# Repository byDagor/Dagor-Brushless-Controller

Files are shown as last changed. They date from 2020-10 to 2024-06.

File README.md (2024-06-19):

# Dagor Brushless Controller

The Dagor Controller is a fully integrated tiny solution for brushless-based actuators with wireless capabilities and three operation modes: angular position, velocity and torque. It is an ESP32-based brushless controller that has an on-board magnetic encoder, a three-phase MOSFET driver, three MOSFET half-bridges, a temperature sensor and current sensing resistors.

> 📢 DOCUMENATION WEBSITE: https://docs.dagor.dev/

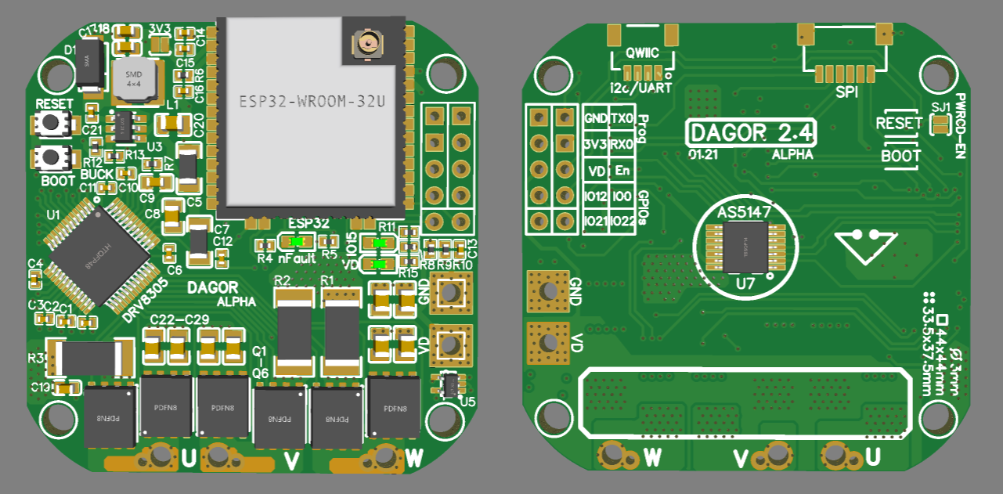
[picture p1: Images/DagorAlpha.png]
DagorBoard


## Key specs
| Specification | Rating |
| --- |:---:|
| Dimensions | 44 x 44mm |
| Mass | 12g |
| Power source voltage | 5-24V |
| Peak rms current | up to 40A |
| Magnetic sensor resolution | 14 bits |
| Temperature sensor range | -10 ~ 120°C |

> Note: The project is STILL currently on it’s Alpha stage and with the help of the Alpha testers the project will move forward faster.

## What makes this Controller different?
The *Dagor Brushless Controller* was designed as a simple platform for hobbyist and students to power brushless-based projects. This board offers wired and wireless connectivity modes to accommodate a variety of different kinds of projects. The firmware for this board was developed for the Arduino development environment and powered by the [SimpleFOC project](simplefoc.com). This code is merely a starting point as it’s encouraged to modify it to fit specific projects. The firmware being very easy to modify and understand gives some key advantages:

- great platform for single board projects
- custom communication schemes for multi-board projects
- implementation of unique control laws
- endless amount of compatible libraries

## HW Revisions
| Reivision | Changes |
| --- |:---:|
| 2.7 | Solid GND plane, input TVS diode. |
| 2.6 | Rearrenged the LEDs to avoid bleed, added extra bulk capacitance to the back. |

## Firmware Roadmap
- [x] Torque/ current control mode
- [ ] PWM input control
- [x] Full fault diagnostics report
- [ ] DRV8305 communication library
- [ ] Deep-sleep mode
- [ ] Save calibration parameters in ESP32's EEPROM
- [ ] Stall detection algorithm
- [ ] Finish RS-485-based protocol, directional comms working
- [ ] Virtual walls algorithm
- [ ] Detect DRV warnings vs. errors
- [ ] Make nicer out of bounds behavior
- [ ] Finish implementing state machine
- [ ] Change "H" homing command to accept home as arbitrary number or current position
- [ ] OTA Update
- [ ] Status LED blink patterns

## Contact
david@simplefoc.com 
[Linkedin](https://www.linkedin.com/in/david-g-reyes/)  
[YouTube](https://www.youtube.com/channel/UC4gsPZan2T4v5LpJ5J_t7sQ/featured)

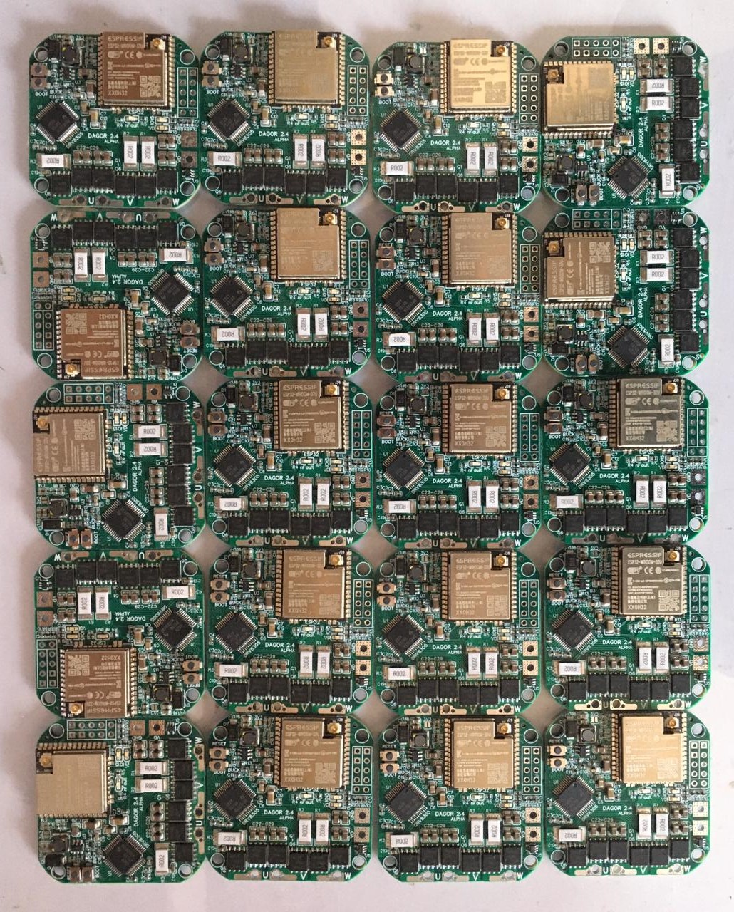
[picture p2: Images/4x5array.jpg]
array


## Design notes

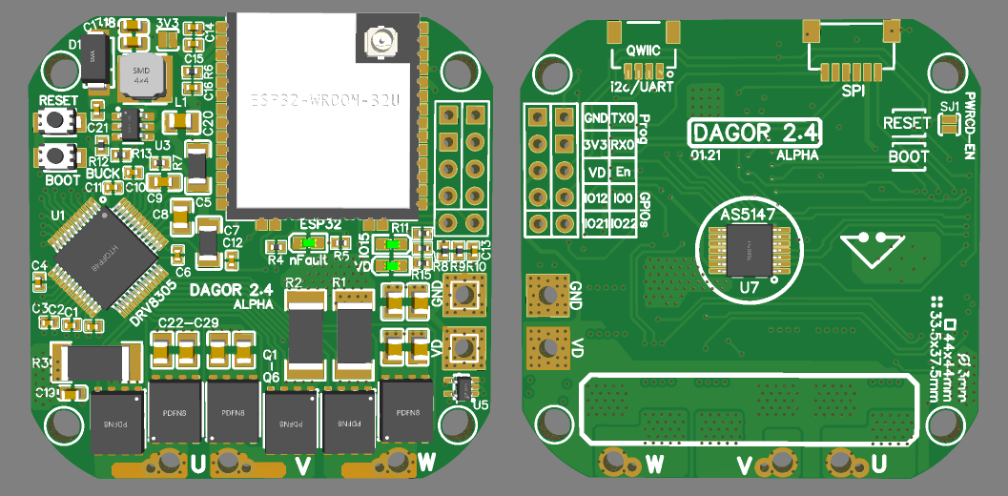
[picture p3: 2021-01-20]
Images/DagorAlpha2.4.png

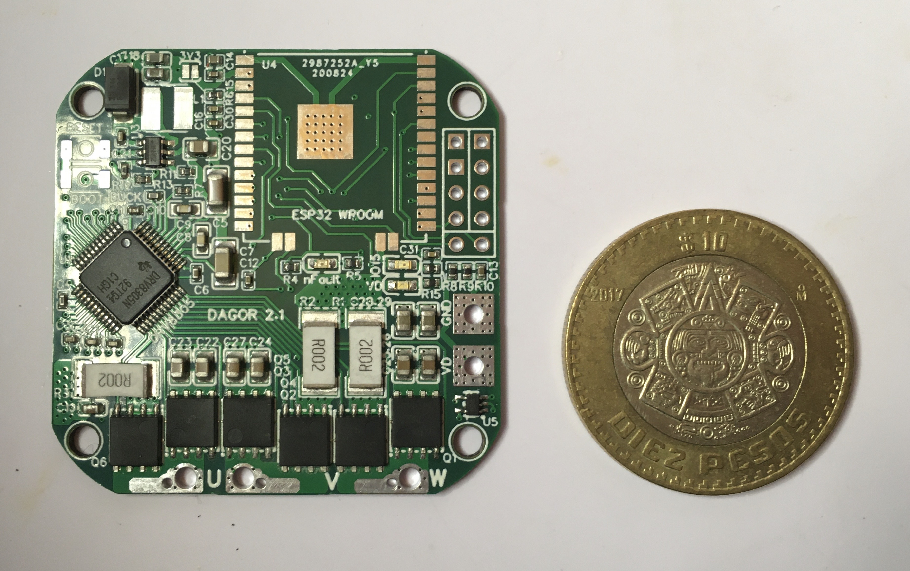
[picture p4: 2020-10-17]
Images/Size reference.JPG

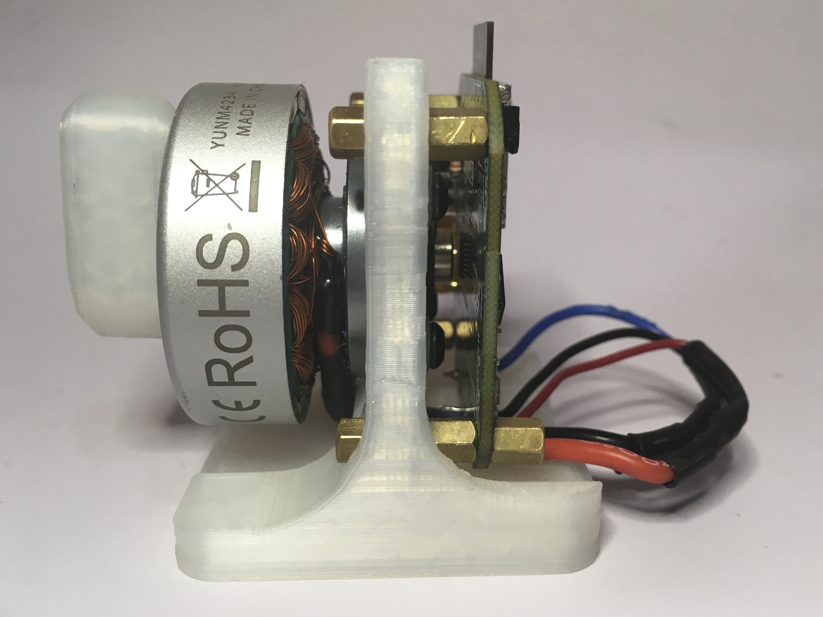
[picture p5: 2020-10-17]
Images/Side View.JPG

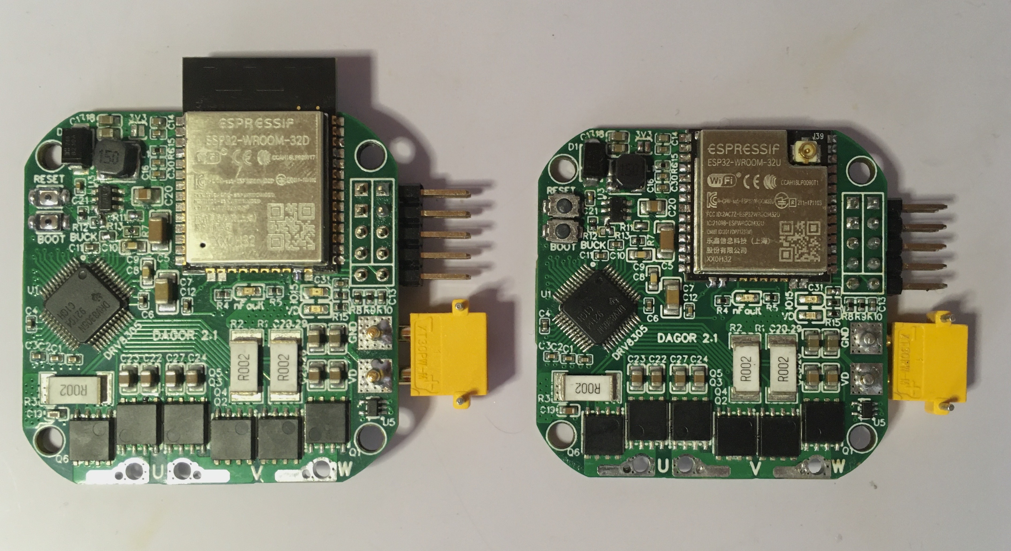
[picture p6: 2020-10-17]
Images/ESP32 Wroom U and D.JPG

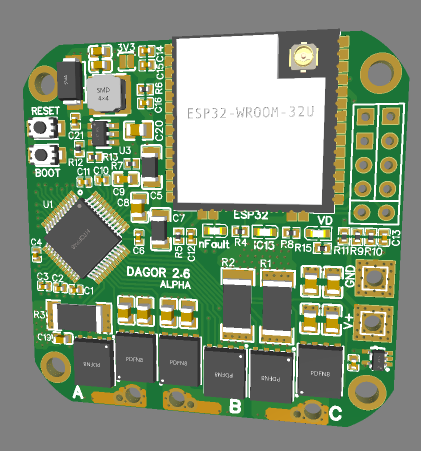
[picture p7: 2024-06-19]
Images/Dagor 2.6.PNG

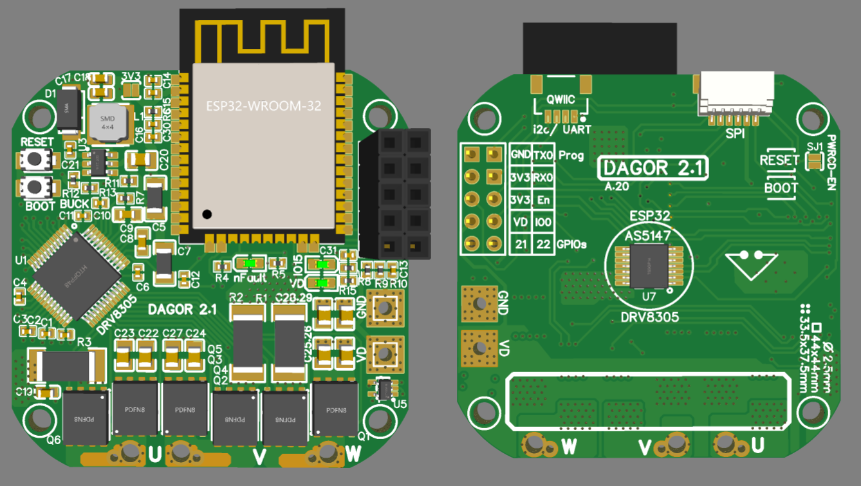
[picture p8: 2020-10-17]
Images/Dagor2.1.png

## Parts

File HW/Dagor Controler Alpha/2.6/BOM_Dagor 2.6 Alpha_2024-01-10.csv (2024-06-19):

ID | Name | Designator | Footprint | Quantity | Manufacturer Part | Manufacturer | Supplier | Supplier Part | Price
1 | 1nF | C1,C2,C3,C13 | C0402 | 4 | 0402B102K500NT | FH | LCSC | C1523 | 0.001
2 | 1uF | C4,C6,C10,C11 | C0402 | 4 | CL05A105KA5NQNC | SAMSUNG | LCSC | C52923 | 0.004
3 | 4.7uF | C5 | C1206 | 1 | 1206B475K500NT | FH | LCSC | C29823 | 0.031
4 | 2.2uF | C7 | C1206 | 1 | CL31B225KBHNNNE | SAMSUNG | LCSC | C50254 | 0.027
5 | 47nF | C8 | C0805 | 1 | CL21B473KCFNNNE | SAMSUNG | LCSC | C17074 | 0.02
6 | 47nF | C9 | C0603 | 1 | CL10B473KB8NNNC | SAMSUNG | LCSC | C1622 | 0.005
7 | 100nF | C12,C15,C16,C21,C30 | C0402 | 5 | CL05B104KO5NNNC | SAMSUNG | LCSC | C1525 | 0.001
8 | 10uF | C14 | C0402 | 1 | CL05A106MQ5NUNC | SAMSUNG | LCSC | C15525 | 0.005
9 | 22uF | C17 | C0603 | 1 | CL10A226MQ8NRNC | SAMSUNG | LCSC | C59461 | 0.008
10 | 10uF | C18 | C0603 | 1 | CL10A106MA8NRNC | SAMSUNG | LCSC | C96446 | 0.018
11 | 1uF | C19 | C0603 | 1 | CL10A105KB8NNNC | SAMSUNG | LCSC | C15849 | 0.005
12 | 10uF | C20,C22,C23,C24,C25,C26,C27,C28,C29,C31,C32,C33,C34,C35,C36,C39 | C0805 | 16 | GRM21BR61H106KE43L | Murata Electronics | LCSC | C440198 | 0.071
13 | 10uF | C37,C38 | C1206 | 2 | 1206X106M500NT | Guangdong Fenghua Advanced Tech | LCSC | C170075 | 0.045
14 | B230A-13-F | D1 | SMA_L4.4-W2.6-LS5.0-RD | 1 | B230A-13-F | DIODES | LCSC | C12889 | 0.072
15 | 15uH | L1 | IND-SMD_L4.0-W4.0 | 1 | PIS3D18P-150M-T | EMTEK | LCSC | C251755 | 0.228
16 | RED | LED1 | LED0603-R-RD | 1 | KT-0603R | KENTO | LCSC | C2286 | 0.006
17 | Blue | LED2 | LED0603-R-RD | 1 | 19-217/BHC-ZL1M2RY/3T | EVERLIGHT | LCSC | C72041 | 0.018
18 | Yellow | LED3 | LED0603-R-RD | 1 | 19-213/Y2C-CQ2R2L/3T(CY) | EVERLIGHT | LCSC | C72038 | 0.021
19 | TPH4R008 | Q1,Q2,Q3,Q4,Q5,Q6 | POWERVDFN-8_L6.2-W5.2-P1.27-LS6.0-BL | 6 | TPH4R008NH,L1Q(M | TOSHIBA | LCSC | C396039 | 1.22
20 | 0.002 | R1,R2,R3 | R2512 W/ KELVIN | 3 | MS122WF200NT4E | UniOhm | LCSC | C60923 | 0.095
21 | 330 | R4,R8 | R0402 | 2 | 0402WGF3300TCE | UniOhm | LCSC | C25104 | 0.001
22 | 10K | R5,R6,R11 | R0402 | 3 | 0402WGF1002TCE | UniOhm | LCSC | C25744 | 0.001
23 | 100 | R7 | R0402 | 1 | 0402WGF1000TCE | UniOhm | LCSC | C25076 | 0.001
24 | 33K | R9 | R0402 | 1 | 0402WGF2402TCE | UniOhm | LCSC | C25769 | 0.001
25 | 3.3K | R10 | R0402 | 1 | 0402WGF3301TCE | UniOhm | LCSC | C25890 | 0.001
26 | 110K | R12 | R0402 | 1 | NQ02WGF1103TCE | Uniroyal Elec | LCSC | C270379 | 0.002
27 | 33K | R13 | R0402 | 1 | 0402WGF3302TCE | UniOhm | LCSC | C25779 | 0.001
28 | 2.2K | R15 | R0402 | 1 | 0402WGF2201TCE | UniOhm | LCSC | C25879 | 0.001
29 | BOOT | SW1 | SW2-2.6-3.0X2.5X1.2+0.4MM | 1 | TS342A2P-WZ | SHOU HAN | LCSC | C557591 | 0.032
30 | RESET | SW2 | SW2-2.6-3.0X2.5X1.2+0.4MM | 1 | TS342A2P-WZ | SHOU HAN | LCSC | C557591 | 0.032
31 | DRV8305NPHPR | U1 | HTQFP-48_L7.0-W7.0-P0.50-LS9.0-BL-EP | 1 | DRV8305NPHPR | Texas Instruments | LCSC | C75602 | 254.25
32 | LMR14010ADDCR | U3 | SOT-23-6_L2.9-W1.6-P0.95-LS2.8-BR | 1 | LMR14010ADDCR | Texas Instruments | LCSC | C388174 | 0.934
33 | ESP-WROOM-32 | U4 | ESP-WROOM-32-NO-JTAG | 1 | ESP-WROOM-32 | ESPRESSIF | LCSC | C95209
34 | STLM20W87F | U5 | SOT-323-5_L2.1-W1.3-P0.65-LS2.1-BL | 1 | STLM20W87F | STMicroelectronics | LCSC | C129796 | 1.007
35 | AS5147P-HTSM | U7 | TSSOP-14_L5.0-W4.4-P0.65-LS6.5-BL | 1 | AS5147P-HTSM | Advanced Monolithic Systems | LCSC | C481876 | 21.449

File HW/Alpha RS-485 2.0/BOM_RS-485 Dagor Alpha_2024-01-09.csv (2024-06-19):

ID | Name | Designator | Footprint | Quantity | Manufacturer Part | Manufacturer | Supplier | Supplier Part | Price
1 | 100nF | C1 | C0402 | 1 | CL05B104KO5NNNC | SAMSUNG | LCSC | C1525 | 0.001
2 | 10uF | C2,C3,C4,C5 | C1206 | 4 | 1206X106M500NT | Guangdong Fenghua Advanced Tech | LCSC | C170075 | 0.045
3 | 10uF | C6 | C0402 | 1 | CL05A106MQ5NUNC | SAMSUNG | LCSC | C15525 | 0.005
4 | XT30PW(2+2)-M | CN1,CN2 | CONN-TH_4P-XT30PW-M | 2 | XT30PW(2+2)-M艾迈斯,颜色:黑色,90°焊板,弯针 | null | LCSC | C9900018404
5 | 120Ω | R2 | R0805 | 1 | RMC 0805 120R J N | Tyohm(幸亚电阻) | LCSC | C269726 | 0.004
6 | SP3485EN-L/TR | U1 | SOIC-8_L5.0-W4.0-P1.27-LS6.0-BL | 1 | SP3485EN-L/TR | MaxLinear | LCSC | C8963 | 0.252
7 | External SPI | U6 | CONN-SMD_SM06B-SRSS-TB(LF)(SN) | 1 | SM06B-SRSS-TB(LF)(SN) | JST Sales America | LCSC | C160405 | 0.198

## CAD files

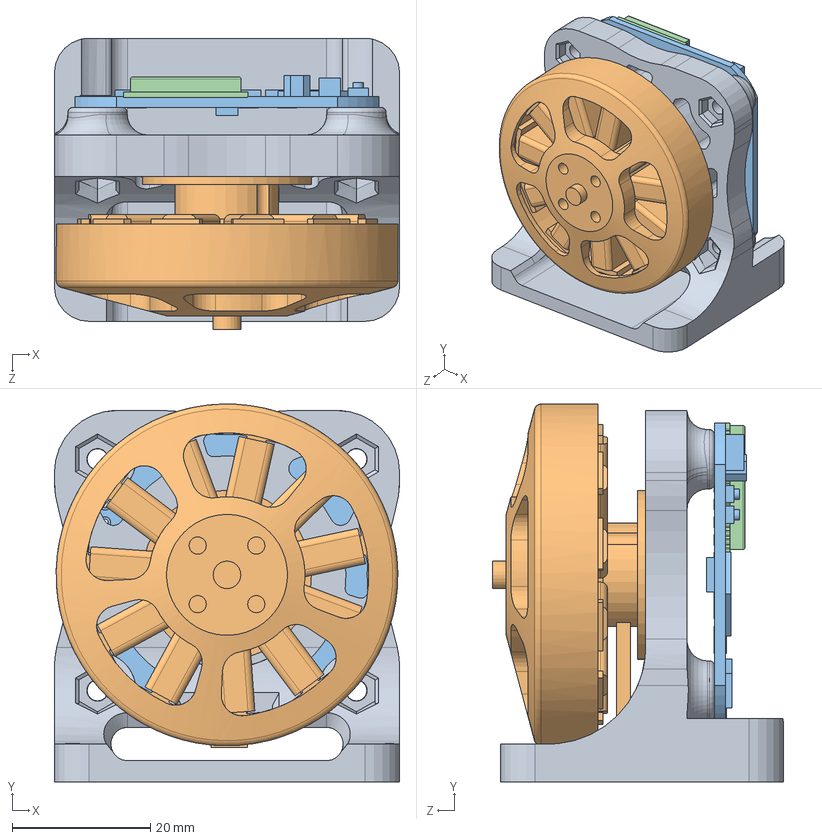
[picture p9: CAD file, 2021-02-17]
CAD/SolidWorks 2020/Dev Kit Assembly 010.SLDASM
50.0 x 54.7 x 42.2 mm
Test Station 2.4.1
BLDC 5010-360KV
Dagor Controller Board 2.4
ESP32-WROOM-32U-

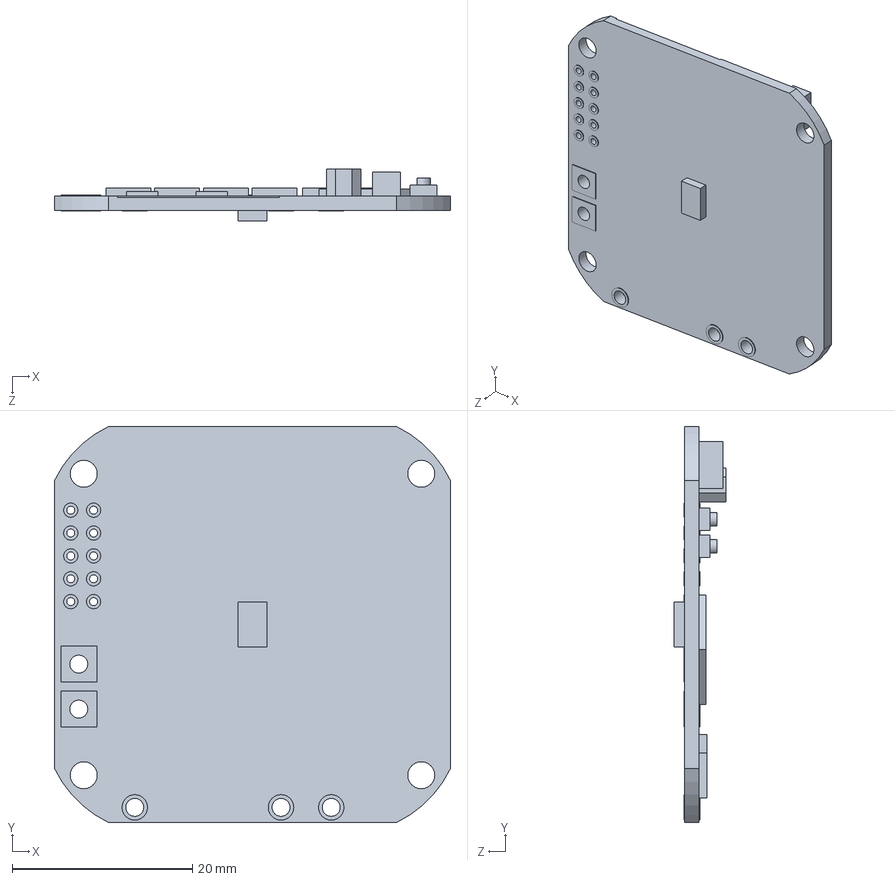
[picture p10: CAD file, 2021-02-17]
CAD/SolidWorks 2020/Dagor Controller Board 2.4.SLDPRT
44.0 x 44.0 x 5.80 mm

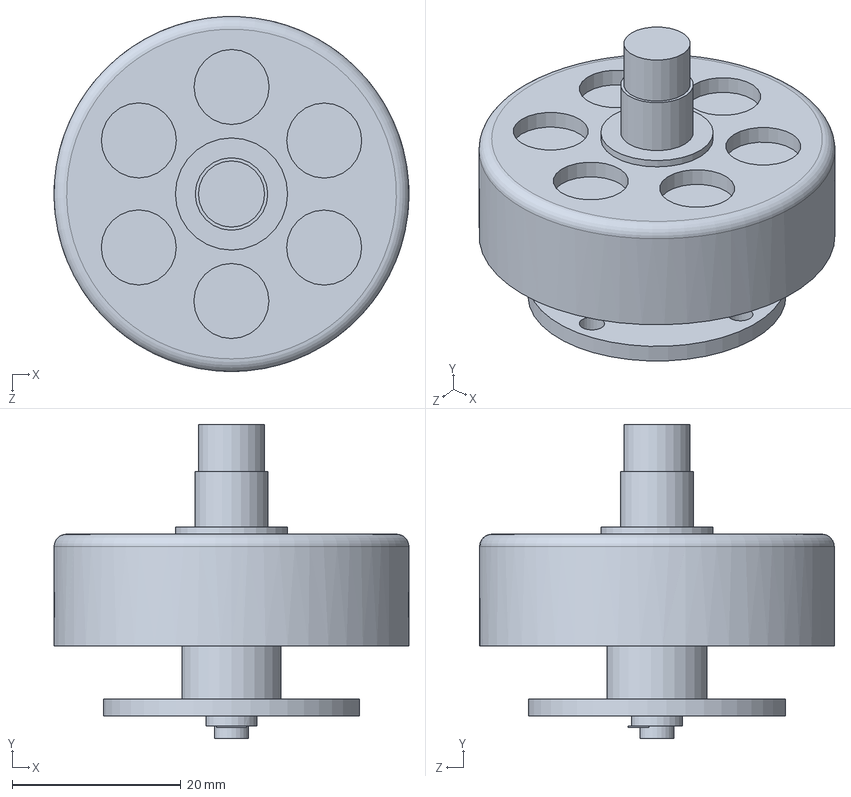
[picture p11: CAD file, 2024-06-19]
CAD/SolidWorks 2022/YUNEEC YUMN4234 B.SLDPRT
42.1 x 37.2 x 42.1 mm

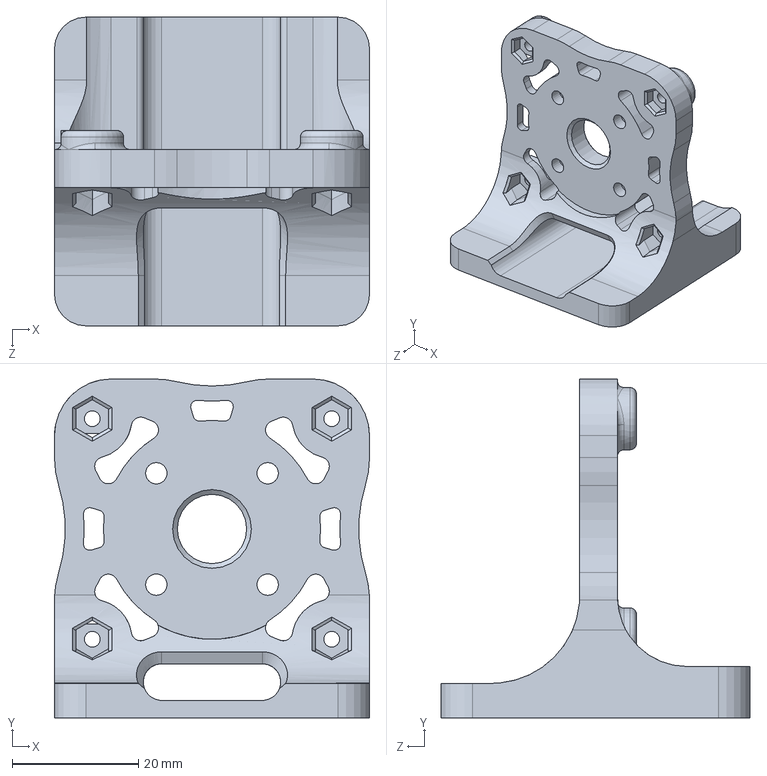
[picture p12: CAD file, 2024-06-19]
CAD/STL/Test Station 2.6 (YUNM + RS485).SLDPRT
50.0 x 53.8 x 49.0 mm

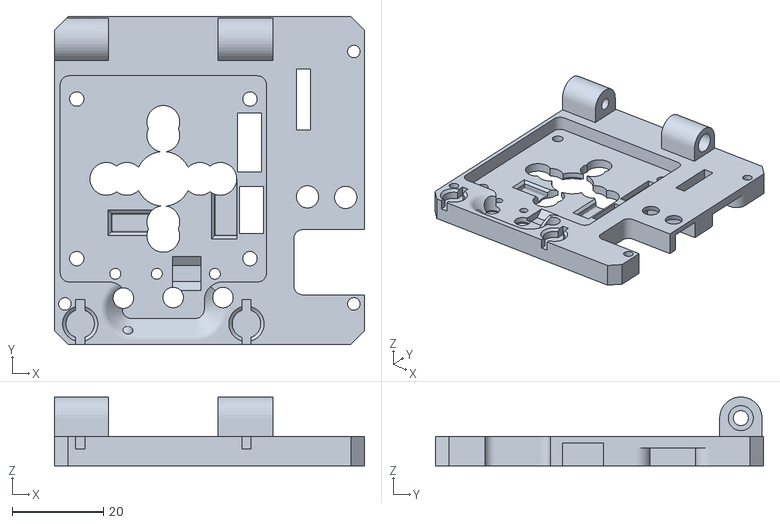
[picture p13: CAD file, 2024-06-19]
HW/Alpha Functional Tester 1.0/CAD/stl/Tester Case A 100.STL
68.0 x 72.0 x 15.1

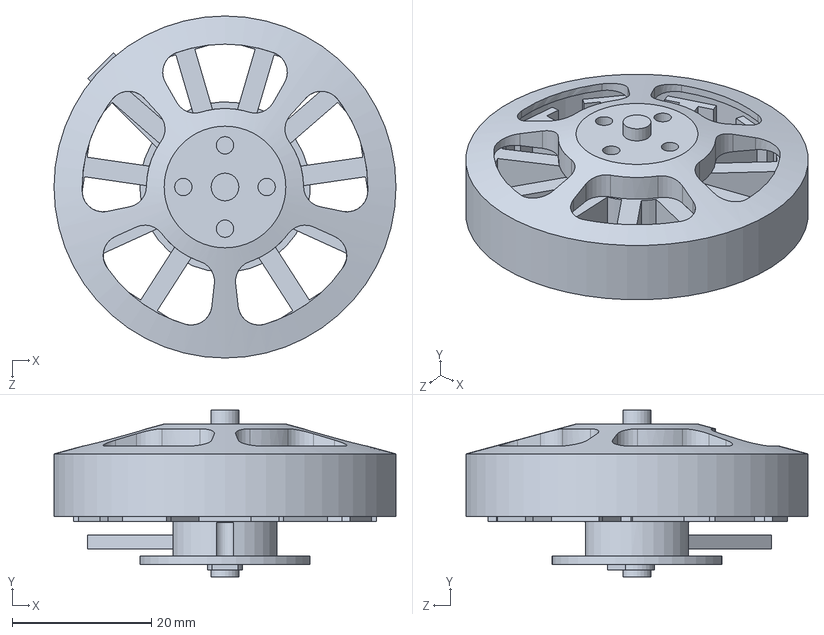
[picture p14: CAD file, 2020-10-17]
CAD/SolidWorks 2016/BLDC 5010-360KV.SLDPRT
49.2 x 24.0 x 49.2 mm

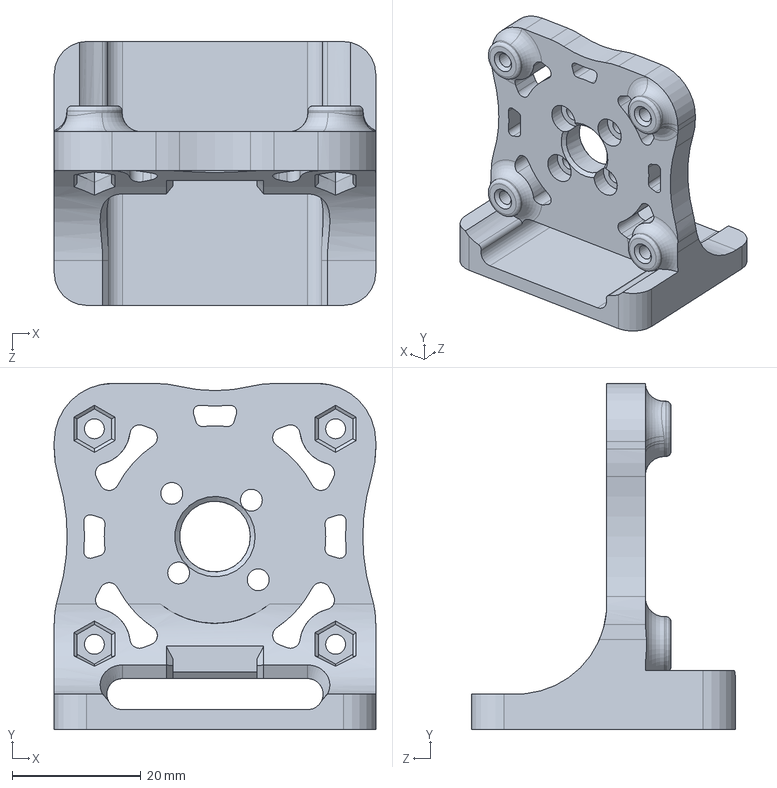
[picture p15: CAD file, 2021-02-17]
CAD/SolidWorks 2020/Test Station 2.4.1.SLDPRT
50.0 x 53.8 x 41.0 mm

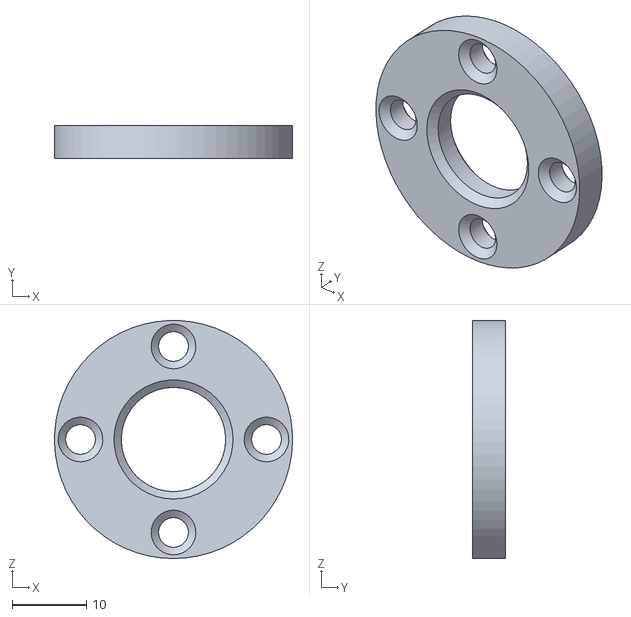
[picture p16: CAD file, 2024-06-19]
HW/Alpha Functional Tester 1.0/CAD/stl/Motor Spacer 100.STL
32.0 x 4.50 x 32.0

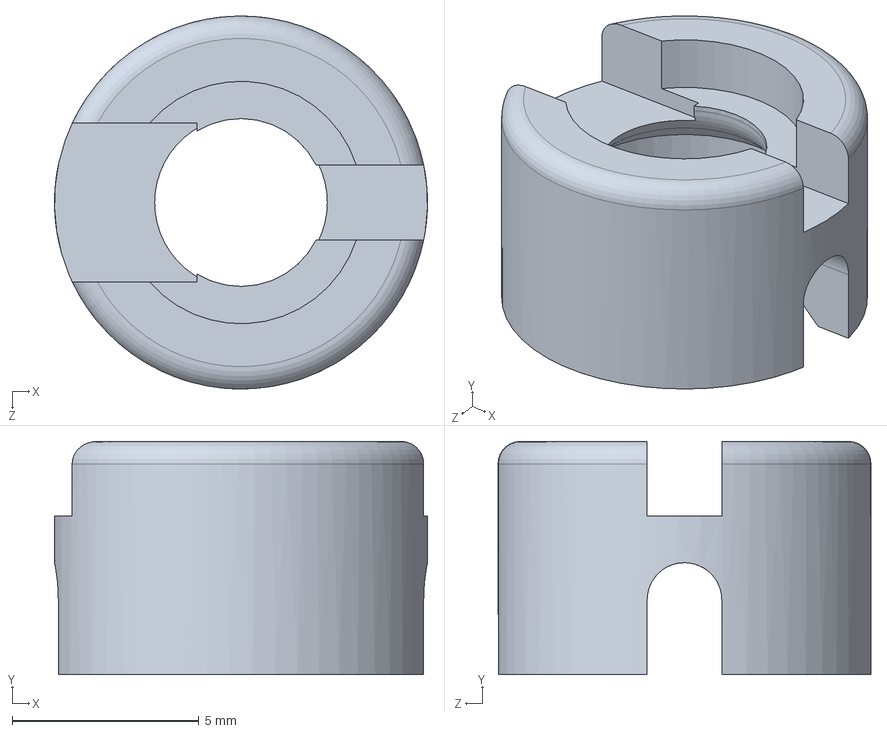
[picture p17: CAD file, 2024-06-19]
HW/Alpha Functional Tester 1.0/CAD/SW2022/Magnet Joint 014.SLDPRT
10.0 x 6.25 x 10.00 mm

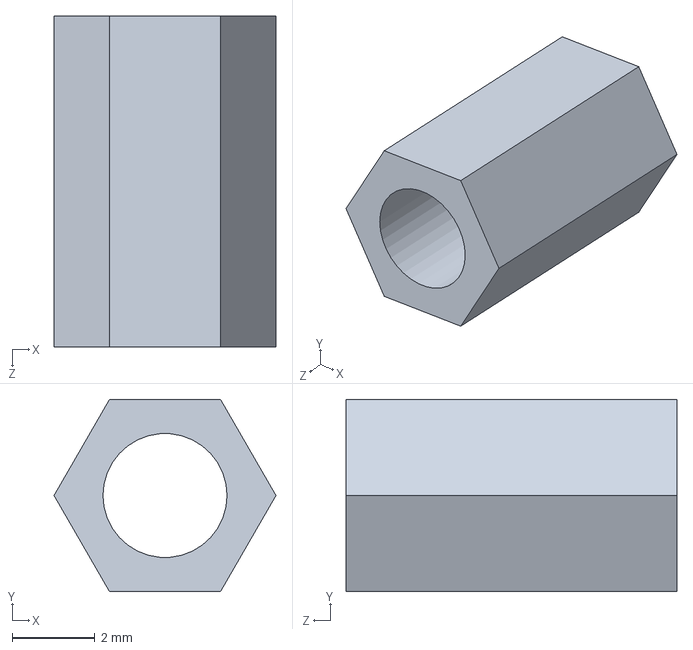
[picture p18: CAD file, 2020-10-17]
CAD/SolidWorks 2016/Stud M3 x 8mm.SLDPRT
5.37 x 4.65 x 8.00 mm

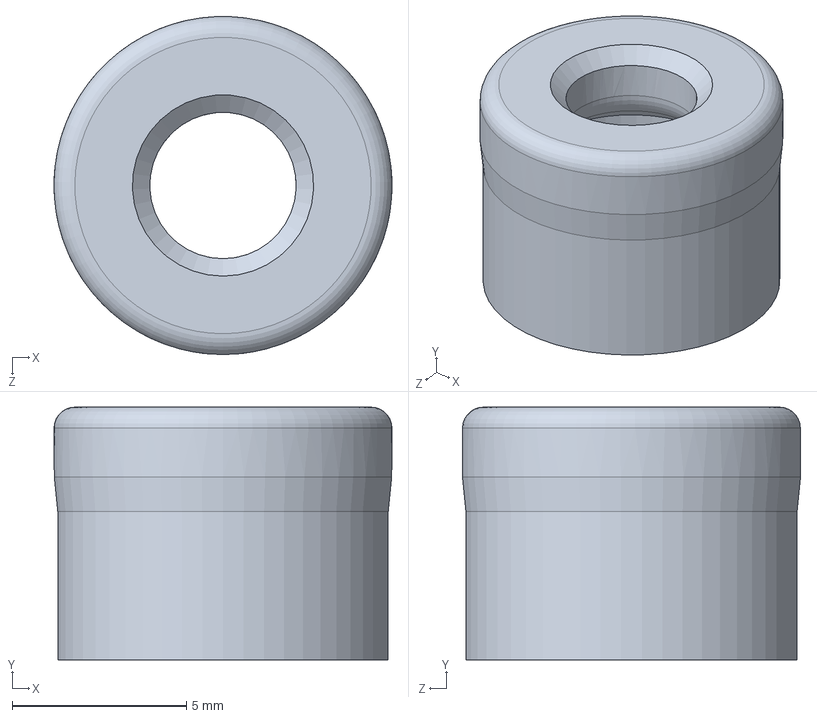
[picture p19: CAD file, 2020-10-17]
CAD/SolidWorks 2022/Magnet Joint 014.SLDPRT
9.70 x 7.25 x 9.70 mm

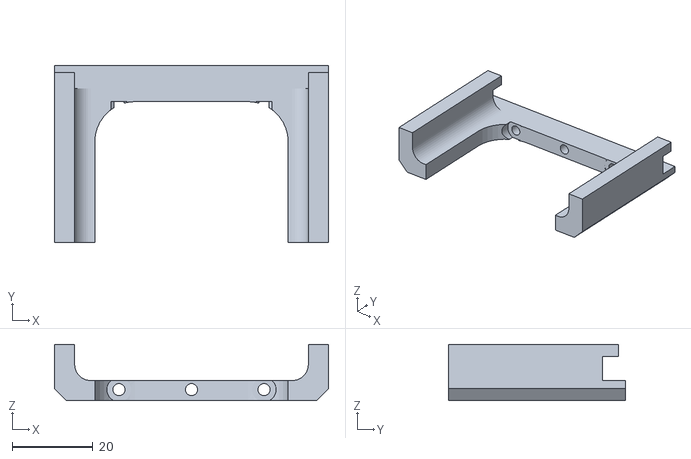
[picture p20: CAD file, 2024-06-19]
HW/Alpha Functional Tester 1.0/CAD/stl/Tester Case C 100.STL
68.0 x 44.0 x 14.0

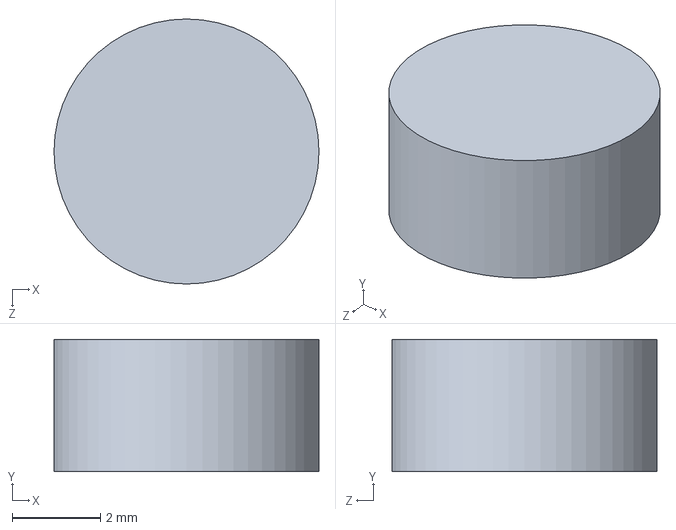
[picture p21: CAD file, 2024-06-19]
HW/Alpha Functional Tester 1.0/CAD/SW2022/Diametrical Magnet 6x3mm.SLDPRT
6.00 x 3.00 x 6.00 mm

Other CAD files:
CAD/SolidWorks 2016/ESP-WROOM-32.sldprt
CAD/SolidWorks 2022/Test Station 2.1.SLDPRT
CAD/STL/Dagor Controller Board 2.4.STL
CAD/STL/Test Station 2.4.1.STL
CAD/STL/BLDC 5010-360KV.STL
CAD/STL/ESP32-WROOM-32U-.STL
CAD/STL/Test Station 2.6 (YUNM + RS485).STL
CAD/SolidWorks 2016/Dagor PCB 2.1.SLDPRT
CAD/SolidWorks 2016/Stud M3 x 6mm.SLDPRT
CAD/SolidWorks 2016/Test Station 2.1.SLDPRT
CAD/SolidWorks 2020/BLDC 5010-360KV.SLDPRT
CAD/SolidWorks 2020/ESP32-WROOM-32U-.SLDPRT
CAD/SolidWorks 2022/Diametrical Magnet 6x6mm.SLDPRT
CAD/SolidWorks 2022/Pointer 010.SLDPRT
HW/Alpha Functional Tester 1.0/CAD/SW2022/Motor Spacer 100.SLDPRT
HW/Alpha Functional Tester 1.0/CAD/SW2022/Tester Case A 100.SLDPRT
HW/Alpha Functional Tester 1.0/CAD/SW2022/Tester Case B 100.SLDPRT
HW/Alpha Functional Tester 1.0/CAD/SW2022/Tester Case C 100.SLDPRT
HW/Alpha Functional Tester 1.0/CAD/stl/Magnet Joint 014.STL
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

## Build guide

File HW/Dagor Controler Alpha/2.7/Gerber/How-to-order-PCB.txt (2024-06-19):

How to Order PCB

Please refer to:
https://docs.easyeda.com/en/PCB/Order-PCB

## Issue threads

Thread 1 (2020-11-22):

Gerbers

ethansayre, 2020-11-22:
Hi @byDagor, great work! Do you by chance have the Gerber files you used to make the boards? Or do you have a link to purchase them if you are selling these boards?

Thanks!

byDagor, 2020-11-26:
hi @ethansayre :) I'm doing an alpha run on the newest revision. Would you be interested in buying one?

byDagor, 2020-11-29:
If you want an alpha board please fill this forms: https://forms.gle/mN9Svp7R9zVknNU36

Jaspeh, 2021-03-25:
It looks like it's not possible to buy an alpha board anymore, when will I be able to buy a board? Thanks a lot for your effort, this board will be awesome for hobbyists!

byDagor, 2021-03-26:
I made a small batch of boards and they're on their way to their new homes. After I get a bit feedback I'll have another batch made. :)

samuk, 2021-11-15:
Is this project still being worked on? Could you publish the Kicad/Gerber files, please?

rekabuk, 2022-01-22:
Hi Dagor,
Are you still working on this? I'd like to experiment with some of your boards, when will you be doing the next version?
Would you consider releasing the schematic and PCB files?
Andrew

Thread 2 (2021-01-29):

Hardware Specs...24V?

thieri, 2021-01-29:
Hi, what is the limiting factor for only 24V? I would be in need of 30V (8s Lifepo4 battery)...

byDagor, 2021-02-05:
TESTING! I'm not sure of the hard voltage limit, should be over 34 volts, I just don't have the tools to do a lot of testing and rate the board higher.

thieri, 2021-02-10:
Thanks

Closed 2021-02-10.

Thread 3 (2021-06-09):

Published Schematic

cdrose, 2021-06-09:
Hi, I am looking for a suitable board to run SimpleFOC for a project, your Dagor board is *so close* to meeting all my specs but just not quite the right physical size. Would you consider sharing the schematic so I can create a different shape PCB or are you keeping the PCB design closed source?

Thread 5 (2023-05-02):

Driving 48v BLDC motor with Dagor

atlaste, 2023-05-02:
I'm just going to ask, see what happens...

I've been following these dagor boards for a while now, because I would like to see if I can use SimpleFoc to drive a lathe spindle for FluidNC (I'm a contributor there). I'm specifically wondering if I can get it to do threading - which is a hard task by itself. The fact that your boards use an esp32 might be a nice advantage.

Anyways, I'm aiming at motors like these, and have a 500W one at home to tinker with. They already have an integrated hall sensor, so I suppose it should be possible to use these. https://jkongmotor.en.made-in-china.com/product/iwvGOzhHAaVg/China-NEMA-34-86mm-BLDC-Motor-24V-500W-and-48V-1000W-for-The-Sliding-Door-Assembly.html

I know the Dagor boards use 24v, while these motors are 48v rated. DRV8305 goes to 45v max... So if that's replaced by a DRV8323 and the mosfets by bigger ones, would that do the trick? I was wondering if there are any plans down this road?

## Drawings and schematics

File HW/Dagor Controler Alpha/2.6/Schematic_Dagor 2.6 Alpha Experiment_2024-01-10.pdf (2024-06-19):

## Power Stage Magnetic Position Sensor

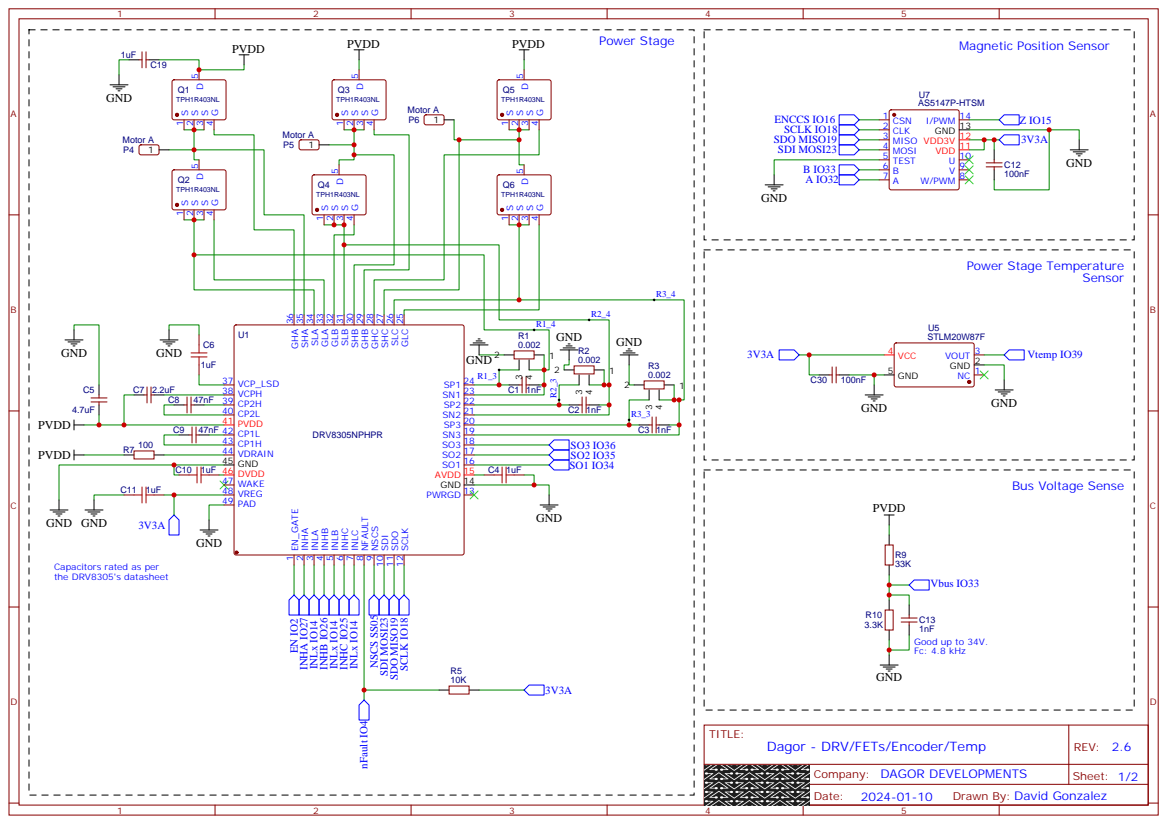
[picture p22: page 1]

GLC 25 SLC 26 SHC 27 GHC 28 GHB 29 SHB 30 SLB 31 GLB 32 GLA 33 SLA 34 SHA 35 GHA 36

Capacitors rated as per

Drawn By: David Gonzalez

IO0 25 IO4 26 IO16 27 IO17 28 IO5 29 IO18 30 IO19 31 NC 32 IO21 33 RXD0 34 TXD0 35 IO22 36 IO23 37 GND 38

## Logic Stage

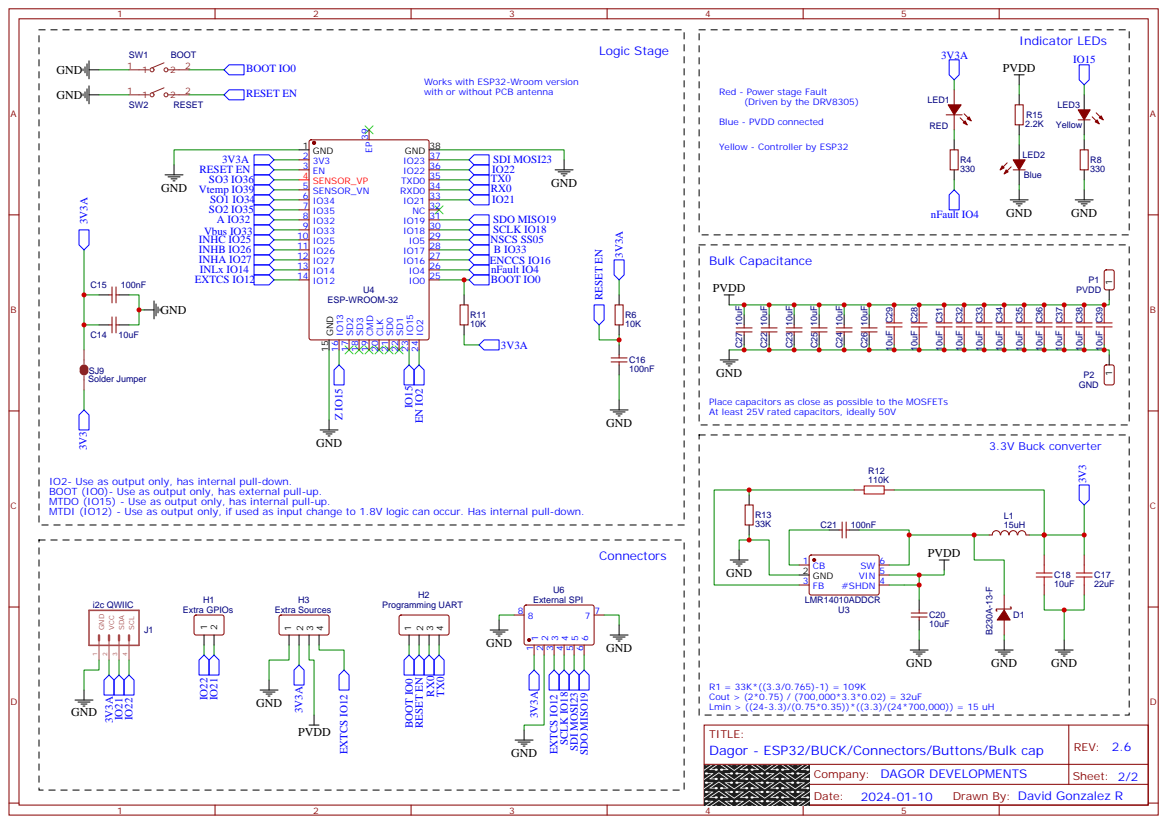
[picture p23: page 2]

Works with ESP32-Wroom version
with or without PCB antenna

Red - Power stage Fault
(Driven by the DRV8305)
Blue - PVDD connected

Place capacitors as close as possible to the MOSFETs
At least 25V rated capacitors, ideally 50V

IO2- Use as output only, has internal pull-down.
BOOT (IO0)- Use as output only, has external pull-up.
MTDO (IO15) - Use as output only, has internal pull-up.
MTDI (IO12) - Use as output only, if used as input change to 1.8V logic can occur. Has internal pull-down.

Drawn By: David Gonzalez R

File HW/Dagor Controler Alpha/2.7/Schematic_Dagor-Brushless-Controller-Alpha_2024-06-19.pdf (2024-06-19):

## Power Stage Magnetic Position Sensor

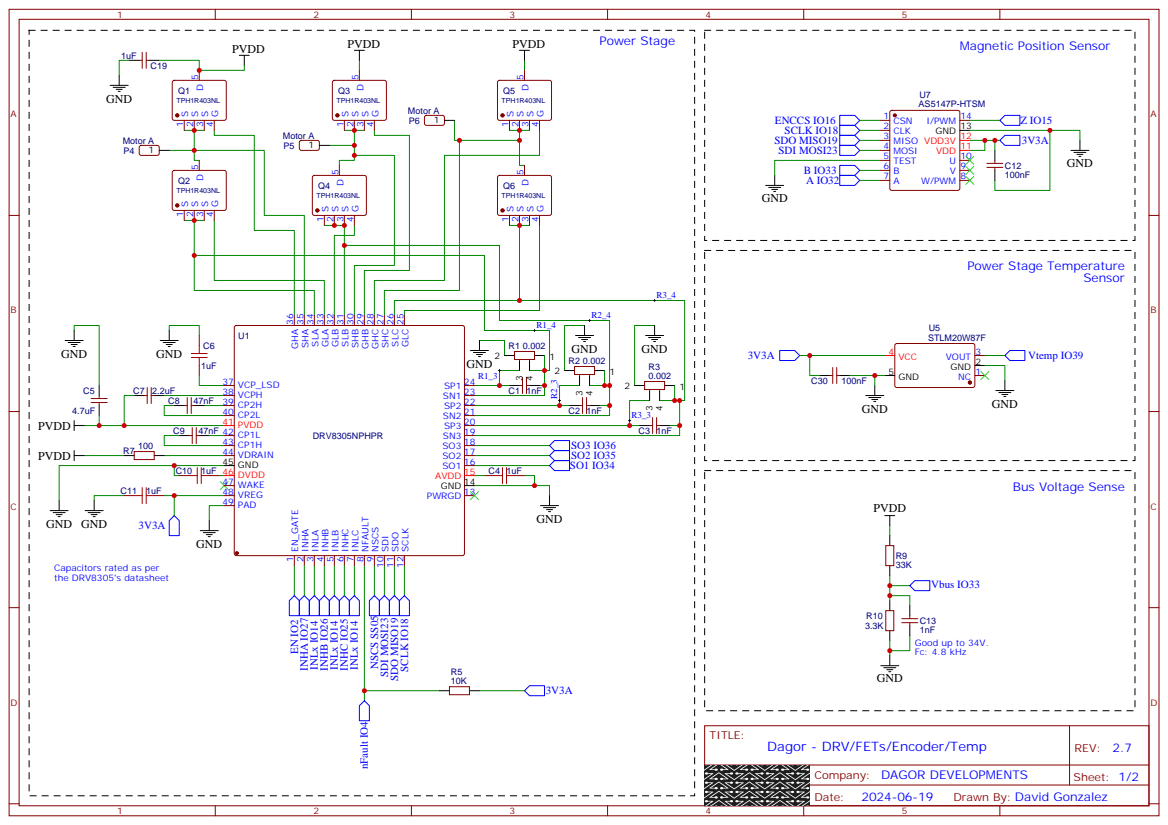
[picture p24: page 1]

GLC 25 SLC 26 SHC 27 GHC 28 GHB 29 SHB 30 SLB 31 GLB 32 GLA 33 SLA 34 SHA 35 GHA 36
PWRGD 13 GND 14 AVDD 15 SO1 16 SO2 17 SO3 18 SN3 19 SP3 20 SN2 21 SP2 22 SN1 23 SP1 24

Capacitors rated as per

Drawn By: David Gonzalez

IO0 25 IO4 26 IO16 27 IO17 28 IO5 29 IO18 30 IO19 31 NC 32 IO21 33 RXD0 34 TXD0 35 IO22 36 IO23 37 GND 38

## Logic Stage

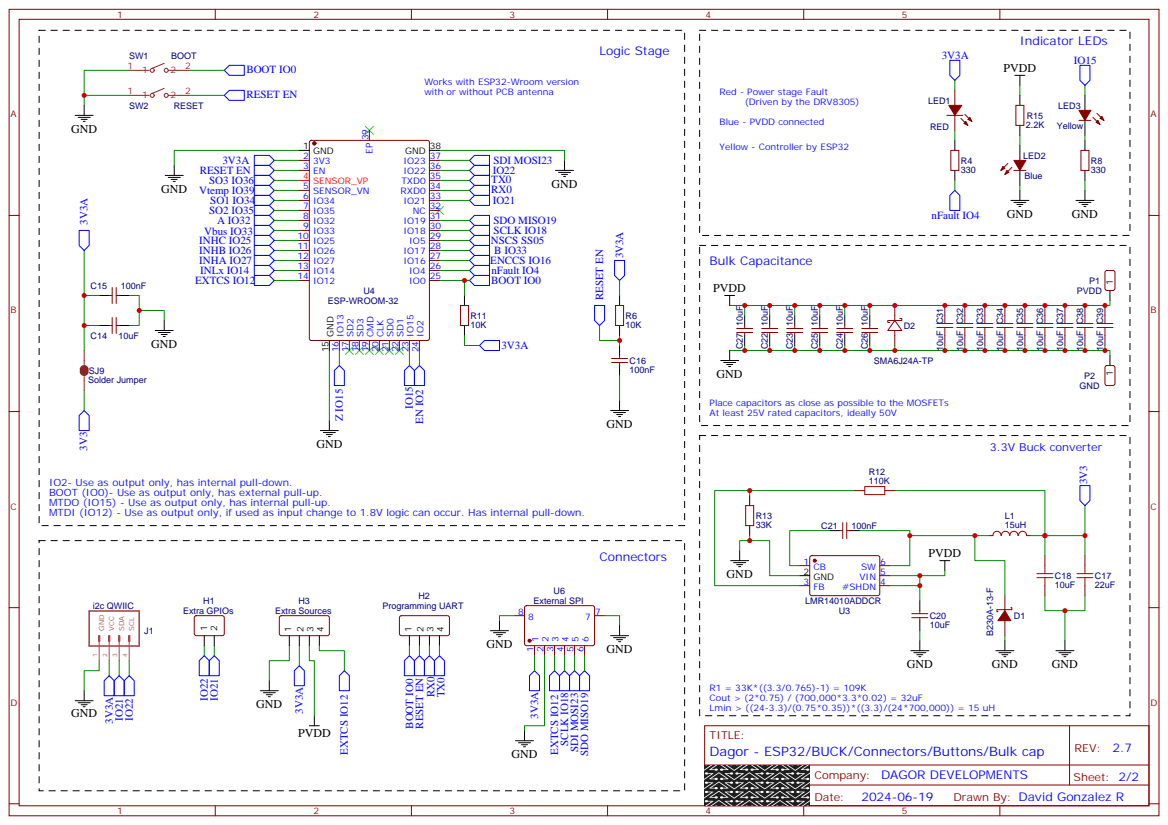
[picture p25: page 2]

Works with ESP32-Wroom version
with or without PCB antenna

Red - Power stage Fault
(Driven by the DRV8305)
Blue - PVDD connected

Place capacitors as close as possible to the MOSFETs
At least 25V rated capacitors, ideally 50V

IO2- Use as output only, has internal pull-down.
BOOT (IO0)- Use as output only, has external pull-up.
MTDO (IO15) - Use as output only, has internal pull-up.
MTDI (IO12) - Use as output only, if used as input change to 1.8V logic can occur. Has internal pull-down.

Drawn By: David Gonzalez R

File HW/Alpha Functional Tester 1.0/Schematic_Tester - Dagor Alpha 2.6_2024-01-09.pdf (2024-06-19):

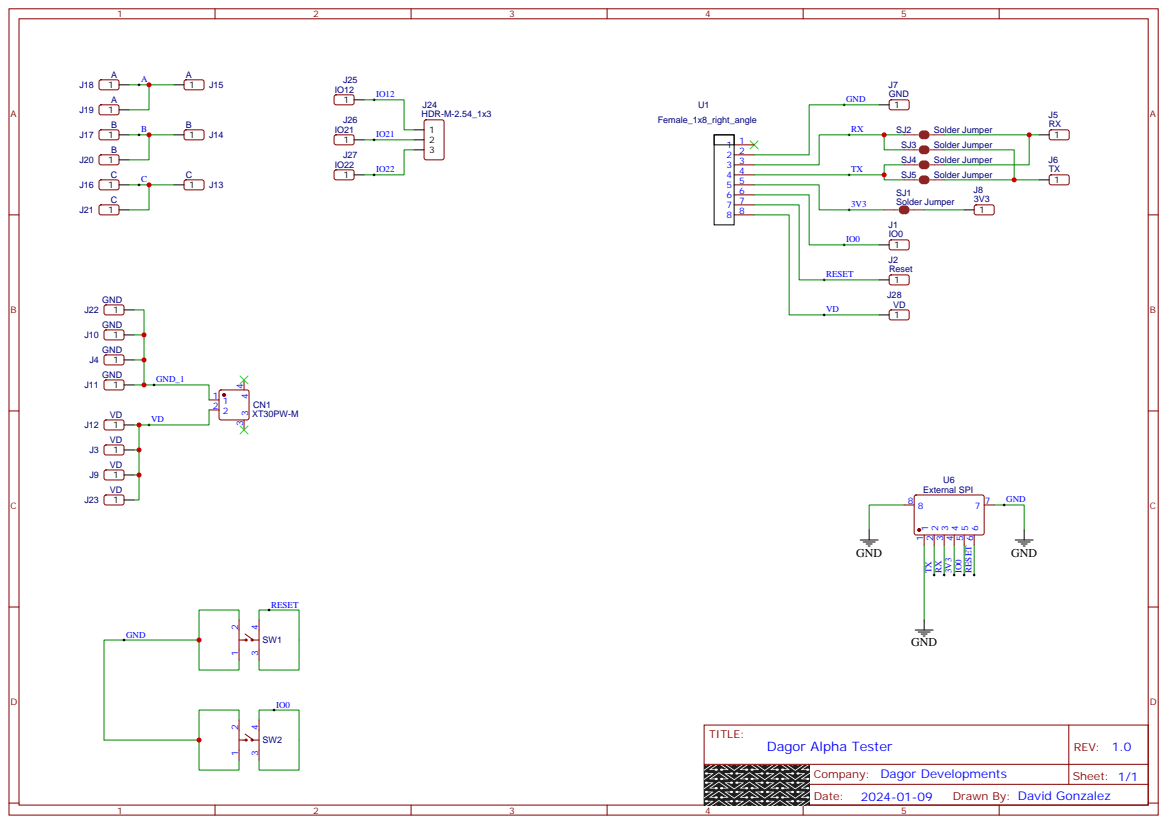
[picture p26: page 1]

Drawn By: David Gonzalez

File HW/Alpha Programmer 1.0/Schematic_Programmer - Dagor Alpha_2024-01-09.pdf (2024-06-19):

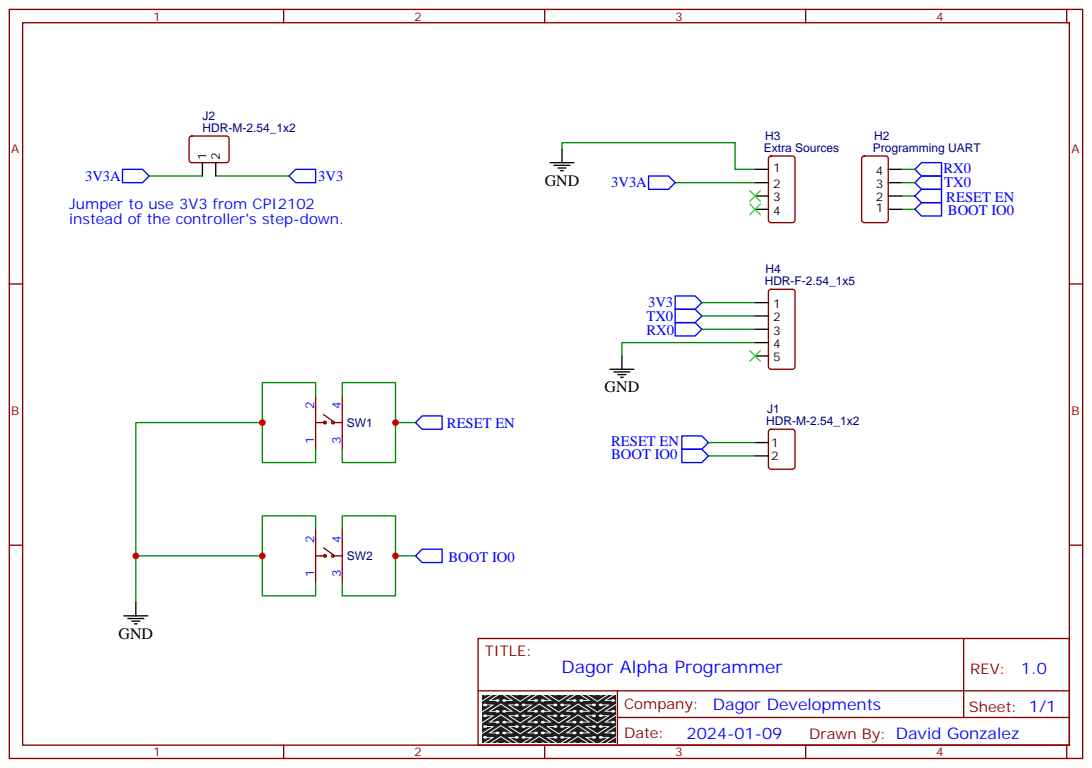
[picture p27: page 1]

Jumper to use 3V3 from CPI2102
instead of the controller's step-down.

Drawn By: David Gonzalez

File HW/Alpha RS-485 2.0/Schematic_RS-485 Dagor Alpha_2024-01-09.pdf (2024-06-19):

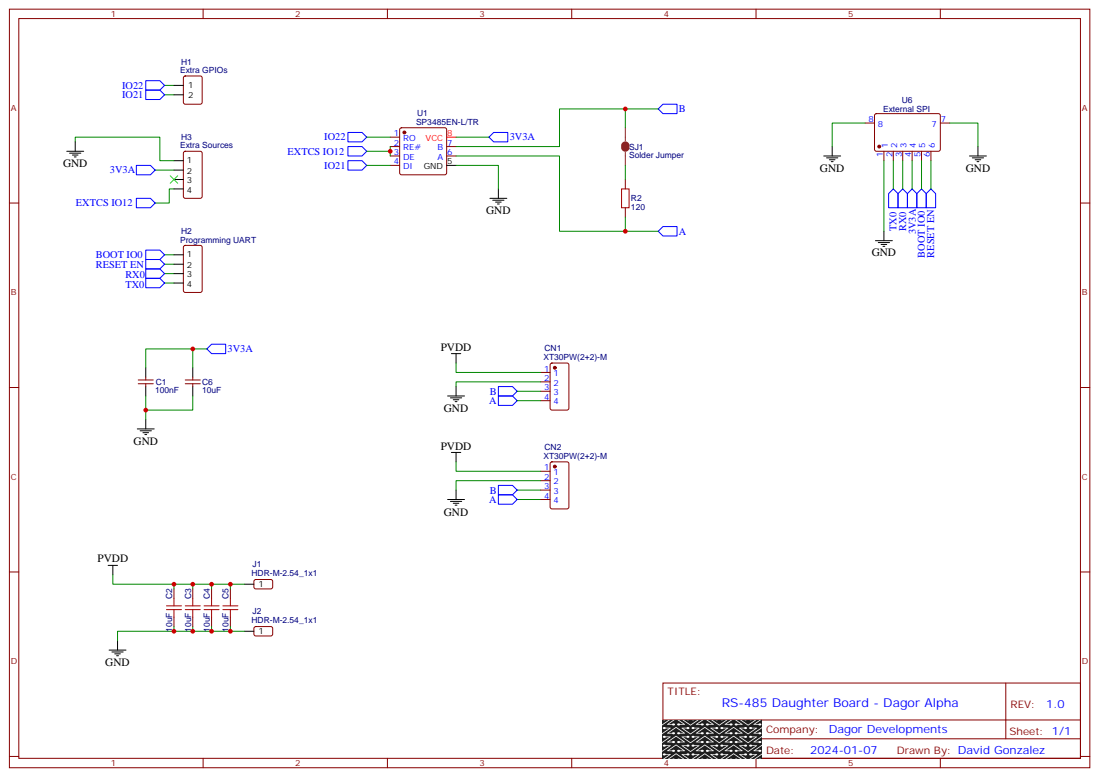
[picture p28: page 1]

Drawn By: David Gonzalez

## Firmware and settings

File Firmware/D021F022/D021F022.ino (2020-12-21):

//Dagor 2.1 Brushless Controller Firmware 022 (Includes current sensing, not yet used for control)

//SimpleFOC Version 2.0.1
#include <SimpleFOC.h>
#include <SPI.h>
#include "driver/mcpwm.h"
#include "soc/mcpwm_reg.h"
#include "soc/mcpwm_struct.h"

//#######_USER VARIABLES_#######
byte pp = 7;                  //BLDC motor number of pole pairs
float phaseRes = 0.560;       //Phase winding resistance [ohms]
byte sourceVoltage = 12;      //Voltage of your power source [Volts]
byte maxCurrent = 2;          //Rough approximation of max current [Amps]

//#######_CONTROLLER PARAMETERS_#######
float ki = 0.002;             //Velocity control loop PROPORTIONAL gain value
float ti = 2.5;               //Velocity control loop INTEGRAL gain value
float lpFilter = 0.000;
float kp = 10;                //Position control loop PROPORTIONAL gain value
float voltageRamp = 25;       //Change in voltage allowed [Volts per sec]
float voltageLimit = phaseRes*maxCurrent;
float velocityLimit = 2000;   //Velocity limit [rpm]

//#######_DRV8305_########
//Datasheet: www.ti.com/lit/ds/symlink/drv8305.pdf
#define enGate 2       //Chip Enable
#define nFault 4       //Fault reading
#define cs 5           //DRV8305 Chip-select
#define so1 36
#define so2 35
#define so3 34
bool faultTrig = false;

//####_CURRENT READING_####
static mcpwm_dev_t *MCPWM[2] = {&MCPWM0, &MCPWM1};
static portMUX_TYPE mcpwm_spinlock = portMUX_INITIALIZER_UNLOCKED;
int a1, a2, a3;         //Current readings from internal current sensor amplifiers
static void IRAM_ATTR isr_handler(void*);
byte currentState = 1;

//######_AS5147_######
#define sensorCS 16             //AS5147 Chip-select
//A and B encoder inputs
//#define arduinoInt1 32             // interrupt 0
//#define arduinoInt2 33             // interrupt 1

//######_TEMPERATURE SENSOR_######
#define vTemp 39
byte maxTemp = 80;      //Maximum temperature [°C]

//#####_TIME MANAGEMENT_#####
float runTime, prevT = 0, timeDif, stateT;
int timeInterval = 1000, totalTempTime;

//####_SIMPLEFOC INSTANCES_####
BLDCMotor motor = BLDCMotor(pp);   //BLDCMotor instance
BLDCDriver3PWM driver = BLDCDriver3PWM(25, 26, 27);     //3PWM Driver instance
MagneticSensorSPI sensor = MagneticSensorSPI(AS5147_SPI, sensorCS);       //SPI Magnetic sensor instance
//Encoder sensor = Encoder(4, 2, 1024);       // Quadrature encoder instance

// Interrupt routine intialisation
// channel A and B callbacks
//void doA(){sensor.handleA();}
//void doB(){sensor.handleB();}

//--------------------------------------------Set-up--------------------------------------------
void setup() {
  Serial.begin(115200);

  analogSetCycles(2);

  //Pinmodes
  pinMode(15,OUTPUT);
  digitalWrite(15,HIGH);
  pinMode(so1, INPUT);
  pinMode(so2, INPUT);
  pinMode(so3, INPUT);
  pinMode(nFault, INPUT);
  pinMode(enGate, OUTPUT);
  digitalWrite(enGate, LOW);

  //SPI start up
  pinMode(cs, OUTPUT);
  digitalWrite(cs, HIGH);
  SPI.begin();
  SPI.setBitOrder(MSBFIRST);
  SPI.setDataMode(SPI_MODE1);

  //Motor driver initialization
  delay(250);
  Serial.println("DRV8305 INIT");
  drv_init();
  delay(500);

  Serial.println("enGate Enabled");
  digitalWrite(enGate, HIGH);
  delay(500);

  //Initialise magnetic sensor hardware
  sensor.init();

  //If using encoder
  //sensor.enableInterrupts(doA, doB); 
  
  //Link the motor to the sensor
  motor.linkSensor(&sensor);
  
  // driver config, power supply voltage [V]
  driver.voltage_power_supply = sourceVoltage;
  driver.init();
  motor.linkDriver(&driver);

  // set FOC loop to be used: ControlType::voltage, velocity, angle
  motor.controller = ControlType::angle;

  // Sensor aligning voltage
  motor.voltage_sensor_align = voltageLimit/2;
  
  // velocity PI controller parameters, default K=0.5 Ti = 0.01
  motor.PID_velocity.P = ki;
  motor.PID_velocity.I = ti;
  motor.PID_velocity.D = 0;
  motor.voltage_limit = voltageLimit;
  motor.LPF_velocity.Tf = lpFilter;
  
  // angle P controller, default K=70
  motor.P_angle.P = kp;
  // maximal velocity of the poisition control, default 20
  motor.velocity_limit = velocityLimit;

  motor.useMonitoring(Serial);      // use monitoring functionality
  motor.init();                     // initialise motor
  motor.initFOC();                  // align sensor/ encoder and start FOC
  //motor.initFOC(4.5,CW);
  Serial.println("Ready BLDC.");
  
  _delay(1000);
  Serial.println(motor.zero_electric_angle);

  MCPWM[MCPWM_UNIT_0]->int_ena.timer0_tep_int_ena = true;//A PWM timer 0 TEP event will trigger this interrupt
  MCPWM[MCPWM_UNIT_0]->int_ena.timer1_tep_int_ena = true;//A PWM timer 1 TEP event will trigger this interrupt
  MCPWM[MCPWM_UNIT_0]->int_ena.timer2_tep_int_ena = true;//A PWM timer 2 TEP event will trigger this interrupt
  mcpwm_isr_register(MCPWM_UNIT_0, isr_handler, NULL, ESP_INTR_FLAG_IRAM, NULL);  //Set ISR Handler
}

//--------------------------------------------Loop--------------------------------------------
void loop() {
  motor.loopFOC();
  motor.move(); // target set by the motor.command()  - or by variable motor.target

  float e = sensor.getAngle();
  //Serial.println(e,4);
  
  motor.command(serialReceiveUserCommand());        //user communication

  //Time managment
  runTime = micros();
  timeDif = runTime - prevT;
  prevT = runTime;
  stateT += timeDif;

  //Functions inside this "if" will execute at a 10hz rate
  if(stateT >= 200000){
    tempStatus();
    faultStatus();
    voltageMonitor();
    Serial.print(a1);
  Serial.print(", ");
  Serial.print(a2);
  Serial.print(", ");
  Serial.println(a3);
  }
  
}

//Temperature status and manager
void tempStatus(){
  static int tFlag;

  //Read voltage from temperature sensor and transform it to °C
  float vOut = analogRead(vTemp);
  float temp = (((vOut*3.3)/4095)-1.8577)/-0.01177;
  //Serial.println(temp,2);
  
  if (temp >= maxTemp && tFlag == false){
    int tempTime = micros();
    totalTempTime += tempTime;

    //If temperature is high for 3 seconds disable DRV
    if(totalTempTime >= 3000000){
      tFlag = true;
      digitalWrite(enGate, LOW);
      Serial.print("enGate Disabled - Temperature protection: ");
      Serial.println(temp);
    }
    
  }
  else if (temp <= maxTemp && tFlag == false){
    totalTempTime = 0;
  }
  
}

void voltageMonitor(){
  int rawVoltage = analogRead(17);
  int bVoltage = rawVoltage * 24/4095;
}

static void IRAM_ATTR isr_handler(void*){
  uint32_t mcpwm_intr_status_0;
  uint32_t mcpwm_intr_status_1;
  uint32_t mcpwm_intr_status_2;
  mcpwm_intr_status_0 = MCPWM[MCPWM_UNIT_0]->int_st.timer0_tep_int_st;
  mcpwm_intr_status_1 = MCPWM[MCPWM_UNIT_0]->int_st.timer1_tep_int_st;
  mcpwm_intr_status_2 = MCPWM[MCPWM_UNIT_0]->int_st.timer2_tep_int_st;
  if(mcpwm_intr_status_0 > 0 && currentState == 1){
    a1 = analogRead(so1);
    currentState = 2; 
  }
  else if(mcpwm_intr_status_1 > 0 && currentState == 2){
    a2 = analogRead(so2);
    currentState = 3;
  }
  else if(mcpwm_intr_status_2 > 0 && currentState == 3){
    a3 = analogRead(so3);  
    currentState = 1;
  }
  MCPWM[MCPWM_UNIT_0]->int_clr.timer0_tep_int_clr = mcpwm_intr_status_0;
  MCPWM[MCPWM_UNIT_0]->int_clr.timer1_tep_int_clr = mcpwm_intr_status_1;
  MCPWM[MCPWM_UNIT_0]->int_clr.timer2_tep_int_clr = mcpwm_intr_status_2;
}

//Configure DRV8305 to desired operation mode
void drv_init(){

  //Set to three PWM inputs mode
  digitalWrite(cs, LOW);
  byte resp1 = SPI.transfer(B00111010);
  byte resp2 = SPI.transfer(B10000110);
  digitalWrite(cs, HIGH);
  //010 10010110
  //010 00000110
  Serial.println(resp1, BIN);
  Serial.println(resp2, BIN);
  
  //DC Calibration for current sensing
  /*
  digitalWrite(cs, LOW);
  int resp3 = SPI.transfer(B01010111);
  int resp4 = SPI.transfer(B00000000);
  digitalWrite(cs, HIGH);
  Serial.println(resp3);
  Serial.println(resp4);

  digitalWrite(cs, LOW);
  int resp5 = SPI.transfer(B01010000);
  int resp6 = SPI.transfer(B00000000);
  digitalWrite(cs, HIGH);
  Serial.println(resp5);
  Serial.println(resp6);
  */

  //Adds delay on the current sense signals
  /*
  digitalWrite(cs, LOW);
  int resp5 = SPI.transfer(B01010000);
  int resp6 = SPI.transfer(B11000000);
  digitalWrite(cs, HIGH);
  Serial.println(resp5);
  Serial.println(resp6);
  */
  
  /*
  digitalWrite(cs, LOW);
  int resp3 = SPI.transfer(B00101000);
  int resp4 = SPI.transfer(B10001000);
  digitalWrite(cs, HIGH);
  Serial.println(resp3);
  Serial.println(resp4);

  digitalWrite(cs, LOW);
  int resp5 = SPI.transfer(B00110000);
  int resp6 = SPI.transfer(B10001000);
  digitalWrite(cs, HIGH);
  Serial.println(resp5);
  Serial.println(resp6);
  */
  
}

//Fault status and manager for the DRV8305
//Datahseet pages 37 and 38
void faultStatus(){
  //Read nFault pin from DRV8305 - LOW == error / HIGH == normal operation
  int fault = digitalRead(nFault);
  
  if(fault == LOW && faultTrig == false){
    Serial.println("Fault detected");
    faultTrig = true;
    //Check warning and watchdog reset (Address = 0x1)
    digitalWrite(cs, LOW);
    byte ft1 = SPI.transfer(B10001000);
    byte ft2 = SPI.transfer(B00000000);
    digitalWrite(cs, HIGH);
    Serial.println("Address = 0x1");
    Serial.println(ft1,BIN);
    Serial.println(ft2,BIN);

    //Check OV/VDS Faults (Address = 0x2)
    digitalWrite(cs, LOW);
    byte ft3 = SPI.transfer(B10010000);
    byte ft4 = SPI.transfer(B00000000);
    digitalWrite(cs, HIGH);
    Serial.println("Address = 0x2");
    Serial.println(ft3,BIN);
    Serial.println(ft4,BIN);

    //Check IC Faults (Address = 0x3)
    digitalWrite(cs, LOW);
    byte ft5 = SPI.transfer(B10011000);
    byte ft6 = SPI.transfer(B00000000);
    digitalWrite(cs, HIGH);
    Serial.println("Address = 0x3");
    Serial.println(ft5,BIN);
    Serial.println(ft6,BIN);

    //Check VGS Faults (Address = 0x4)
    digitalWrite(cs, LOW);
    byte ft7 = SPI.transfer(B10100000);
    byte ft8 = SPI.transfer(B00000000);
    digitalWrite(cs, HIGH);
    Serial.println("Address = 0x4");
    Serial.println(ft7,BIN);
    Serial.println(ft8,BIN);
  }
}

//Utility function enabling serial communication the user
String serialReceiveUserCommand() {
  // a string to hold incoming data
  static String received_chars;
  String command = "";

  while (Serial.available()) {
    // get the new byte:
    char inChar = (char)Serial.read();
    // add it to the string buffer:
    received_chars += inChar;
    // end of user input
    if (inChar == '\n') {
      // execute the user command
      command = received_chars;
      // reset the command buffer 
      received_chars = "";
    }
  }
  return command;
}

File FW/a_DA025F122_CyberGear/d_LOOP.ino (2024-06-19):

//###########################################
//                 LOOP
//###########################################

// Do NOT add delay inside the loop void.


void loop() {
  // These functions have to run as fast as possible
  //motor.move();
  gravityComp();
  
  timeManagement();
  motor.loopFOC();
  
  #ifdef MONITORING
    command.run();
    //motor.monitor();
  #endif 
  
  // Fixed rate functions
  // Functions inside this "if" will execute at a 5hz rate (by default).
  // Uncomment/ comment the functions that you wish to use.
  if(stateT >= 1000000/callerFixedFreq){
    //loopTime();
    stateT = 0;
   
    // Un/ comment the functions bellow that you wish to use.
    tempStatus();           // monitors operating temperature, true argument to print temprature
    faultStatus();          // monitors faults and warnings of the DRV8305
    
    // Print for monitoring -> Uncomment to use.
    //voltageMonitor(true);
    //rotorData(false);          // true -> rotor velocity, false -> rotor position
    //phaseCurrents(false);        // true -> DQspace currents, false -> phase currents
    //phaseVoltages(true);    // true -> DQspace voltages, false -> phase voltages
    //Serial.println();       // if printing to serial monitor uncomment to insert a line break
  
  }
  
}

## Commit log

2020-10-17 Firmware update and CAD files
    [BLDC 5010-360KV.SLDPRT, Dagor PCB 2.1.SLDPRT, Diametrical Magnet 6x6mm.SLDPRT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]
2020-11-30 Alpha run of the board soon
2020-11-30 Alpha run of the board soon!
2020-12-09 README: Flashing the board
2021-01-20 README: temp sensor
2021-02-17 New CAD
    [BLDC 5010-360KV.SLDPRT, BLDC 5010-360KV.STL, Dagor Controller Board 2.4.SLDPRT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]
2021-03-20 Closer to current sensing
2021-03-20 remove url to arduino-foc
2021-03-24 True torque Firmware
2021-05-21 Actuator gravity compensation mode
2021-09-28 Added Actuator FW 1.2.2
2023-12-15 2.5 CAD
2023-12-15 updated 2.5 CAD
2024-01-10 feat: programmer and func tester
    [Drill_NPTH_Through.DRL, Drill_PTH_Through.DRL, Drill_PTH_Through_Via.DRL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]
2024-01-10 feat: Alpha RS-485
    [BOM_RS-485 Dagor Alpha_2024-01-09.csv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]
2024-01-23 feat: DRV fault diagnosis
    [BOM_Dagor 2.6 Alpha_2024-01-10.csv, BOM_RS-485 Dagor Alpha_2024-01-09.csv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]
2024-02-01 oop
    oop
    [BOM_Dagor 2.6 Alpha_2024-01-10.csv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]
2024-02-02 feat: RS-485 input commands proto implementation
    [Diametrical Magnet 6x6mm.SLDPRT, Magnet Joint 014.SLDPRT, Pointer 010.SLDPRT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]
2024-02-05 feat: Alpha tester CAD
    [Diametrical Magnet 6x3mm.SLDPRT, Magnet Joint 014.SLDPRT, Motor Spacer 100.SLDPRT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]
2024-02-06 Finished functional tester
    [Motor Spacer 100.SLDPRT, Motor Spacer 100.STL, Tester Case C 100.SLDPRT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]
2024-02-06 feat: added RS485 Daughter board CAD
2024-02-11 fix current sense pwm sync
    [Magnet Joint 014.SLDPRT, Magnet Joint 014.STL, Tester Case A 100.SLDPRT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]
2024-02-11 fixed QD current limits in sfoc
    [a_DA026F130.ino, c_SIMPLEFOC.ino, e_LOOP.ino]
2024-02-18 lowside current sense patch
2024-02-19 offloaded temp sensor to second core
2024-03-28 maybe fix: watchdog issues
    [a_DA026F130.ino, b_GLOBAL.ino, c_SIMPLEFOC.ino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]
2024-06-19 feat: open source.
    [BOM_Dagor 2.6 Alpha_2024-01-10.csv, BOM_Dagor 2.7 Alpha_2024-06-19.csv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]
